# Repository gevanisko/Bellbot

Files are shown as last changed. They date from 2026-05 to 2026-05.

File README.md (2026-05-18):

# BellBot

This repository contains the hardware design files, documentation, and supporting resources for the BellBot project. BellBot is an autonomous luggage transportation robot intended to use sensing, mapping, wireless control, onboard data storage, and motor control to move luggage through indoor environments.

The hardware in this repository is developed across multiple board revisions. Each version is used to test, validate, and improve different parts of the system, including power regulation, peripheral integration, motor control, communication, and future onboard intelligence.

## Project Overview

The long-term goal of BellBot is to create a robotic luggage transportation system capable of navigating indoor environments. The system is designed around Simultaneous Localization and Mapping (SLAM), LiDAR sensing, inertial measurement, Bluetooth control, onboard logging, and multi-directional motor control.

Early board revisions focus on creating a reliable minimum viable product (MVP). Later revisions are intended to improve size, integration, efficiency, and performance.

## Core Goals

The BellBot hardware is designed to support:

- Autonomous navigation through mapped environments
- LiDAR-based obstacle detection and mapping
- Remote control through Bluetooth or another wireless interface
- Onboard storage for sensor data, logs, and system debugging
- Motor control for movement in a 2D plane
- Multiple regulated voltage rails for sensors, logic, and motors
- Expandability for future sensors, memory, and processing hardware

## Hardware Features

Across the project revisions, the BellBot hardware may include:

| Feature | Purpose |
|---|---|
| STM32 Microcontroller | Main control platform for peripherals, motor control, and system logic |
| LiDAR | 2D scanning for mapping, localization, and obstacle detection |
| IMU | Acceleration, angular velocity, magnetic field, and orientation sensing |
| Bluetooth / Wireless Module | Remote control, debugging, or wireless communication |
| SPI Flash / SD Storage | Onboard storage for sensor data and logs |
| Servo / Motor PWM Outputs | Control signals for the robot drive system |
| 3.3 V Rail | Logic-level supply for MCU and low-voltage peripherals |
| 5 V Rail | Peripheral and module power |
| 8 V Rail | Servo or motor power |
| I2C / SPI / UART / Quad-SPI Breakouts | Expansion for additional sensors, memory, or communication modules |
| Battery Charging and Protection | Portable operation and safe lithium-ion battery use |

Later iterations (V2 and onward) are looking to employ AI accelerated MCU chips (STM32 N6) with a reduced size and mainly using SMT components as opposed to through hole components

## Board Revisions

This repository is intended to support multiple hardware revisions. Each revision may include different component choices, layouts, and design improvements.

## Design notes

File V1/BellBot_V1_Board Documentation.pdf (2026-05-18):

# BellBot V1 Board

George Evanisko

May 2026

## 1 Introduction

The objective of BellBot is to incorporate Simultaneous Localization and Mapping (SLAM) alongside other features in order to achieve luggage transportation typically done by a bellboy. This is a difficult task. Therefore, our team decided to first create a minimum viable product (MVP). This is a prototype that limits the number of features to those necessary to demonstrate the basic functionality of the product. For our team, the following criteria were set for the MVP:

- The product can navigate through a pre-mapped obstacle course using LiDAR
- The product can be remotely controlled using Bluetooth
- The product can store all data from operation in onboard memory for further analysis later
- The product can demonstrate maneuverability in all directions on a 2D plane

In order to achieve the criteria for our MVP, a custom printed circuit board (PCB) was designed. Although it may be possible to accomplish the minimum criteria without the use of a custom PCB by using a breadboard or protoboard, a custom PCB was chosen to provide reliable signal integrity, a cleaner aesthetic, and ease of use.
Our custom PCB uses an STM32 Nucleo-F767ZI development board [1], [2] as the main MCU platform, alongside several commercial off-the-shelf (COTS) through-hole components. These components include an inertial measurement unit (IMU), Light Detection and Ranging (LiDAR) unit, Flash SPI memory card for data storage, HC-05 Bluetooth module, four pulse-width modulation (PWM) 8 V continuous-rotation servo pins, as well as additional Quad-SPI and I2C breakout pins to use as needed. At the end of this section, there are 3D renderings of our board. Through-hole COTS components were used for the first iteration due to their ease of soldering, ease of use, and proven reliability. Future iterations of this board will switch to an STM32 SMT chip and SMT components to reduce board size and remove unwanted components.
The 3D modeling/CAD was done in tandem with the board development, and those contents are not covered in this document. This document serves as a datasheet/guide for anyone using the BellBot board. The sections that follow are: (2) Power Systems, which describes how power is distributed throughout the board; (3) Peripherals, which describes how the featured peripherals are connected and used by our MCU; (4) Software Configuration, which shows the STM32CubeMX model and pin configurations used; and (5) Future Improvements, which focuses on future design improvements.

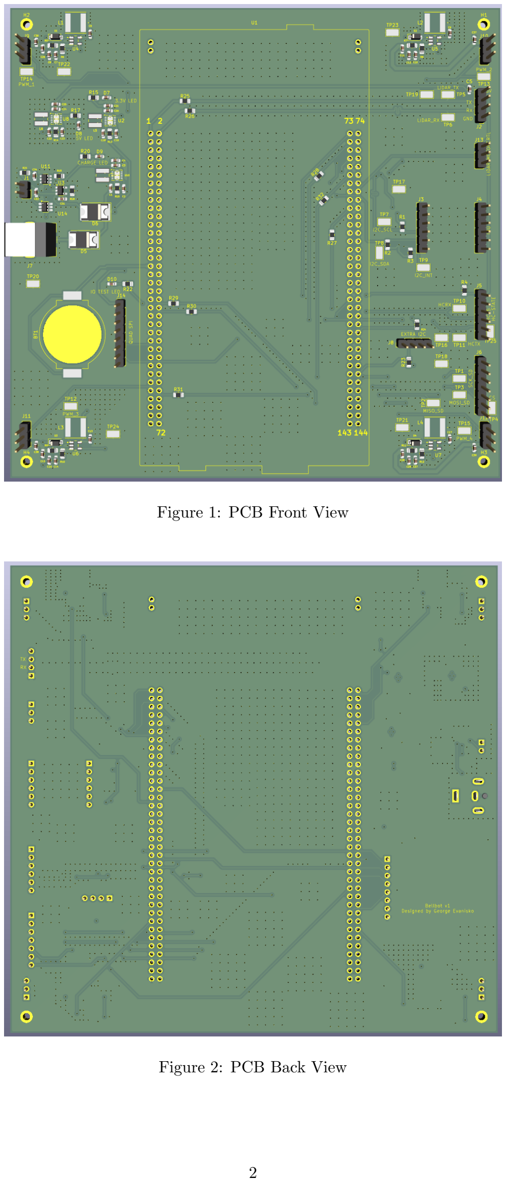
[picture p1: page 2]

Figure 1: PCB Front View

Figure 2: PCB Back View

## 2 Power Systems

Our board features three different voltage levels: 3.3 V, 5 V, and 8 V. The voltage is initially received from a 5 V, 6 A DC power jack input from a wall plug or from a lithium-ion battery. The board uses a simple diode steering method to choose which source to use by employing Schottky diodes to minimize voltage loss. In addition to source control, onboard chips such as the DW01A (U11) [3], along with dual MOSFET FS8205 (U14) [4] chips, are used for battery protection. The board features a separate 5 V charging regulator (U10) that connects directly to the DC power jack and through a lithium-ion charging chip, the MCP73812T (U3) [5], to charge the battery when the DC power jack is being powered by a source greater than the battery’s nominal voltage of 3.3–3.6 V. This means that when using the 5 V, 6 A DC power jack, the battery will always be in charging mode. A table below describes the charging modes:

Mode | DC Power Jack | Battery | Board Operation
DC powered / bat-tery charging | Connected to 5 V wall supply | Charging through the MCP73812T charging circuit | The DC power jack supplies the board power rails while the battery is charged separately. The diode steering circuit pre-vents the battery from being the main supply.
Battery powered | Disconnected | Discharging | The lithium-ion bat-tery supplies the board through the diode steering circuit. The 3.3 V, 5 V, and 8 V rails are generated from the battery input as needed.
Battery protection active | Connected or dis-connected | Protected by DW01A and FS8205 circuit | The protection circuit disconnects or limits the battery path dur-ing unsafe conditions such as over-discharge, overcharge, or overcur-rent. Normal board operation may be interrupted until the fault is removed.

Table 1: Battery and power source operating modes

The U10 5V output regulator is used specifically for charging. The U8 5V output regulator is a general use mainly powering the LiDAR unit.

2.1 8V Boost Converter Inductor and Power Calculations

In terms of power regulators, the board features four 5 V to 8 V switching regulators, each used to power a servo motor. The regulator used is an LT1935 and uses a voltage divider with feedback to determine the output using the following equation:
Vo = 1.265V ∗ (1 + R1
R2
) | (1)

Where R1 and R2 are the resistors used for the feedback voltage divider, as shown by the typical application page:

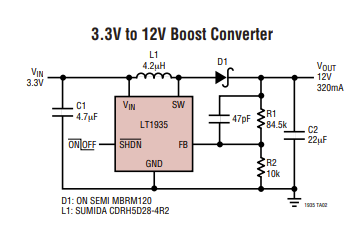
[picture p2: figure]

Figure 3: LT1935 typically application [6]

For our usage, R1 = 56.2K and R2 = 10K yields an output voltage of 8.37 V.
The capacitors are arbitrary and any capacitor can be used if it has a low ESR. The inductor value (L1) is based on the following formula:
L = 3
VIN

VOUT
VOUT − VIN
IMAXf

(2)

Given a maximum switching frequency of 1.2 MHz and an Imax of 2 A with 5 V Vin and 8 V Vout, we can calculate our inductor value as 2.3–2.4 uH, which will be rounded down to 2.2 uH. The output power of the boost converter was also estimated. The output power is related to the input power and converter efficiency, as shown in Equation 3.

POUT = PIN η | (3)

Since input power is equal to input voltage multiplied by input current, this can be written as:

POUT = VIN IIN η | (4)

For this design, the input voltage is 5 V, the maximum input current is approximated using the maximum switch current of 2 A, and the assumed efficiency is 90%.

η = 0.90 | (5)

Substituting the values into Equation 4 gives:

POUT = (5 V)(2 A)(0.90) | (6)
POUT = 9 W | (7)

The output current available from the 8 V rail can then be estimated using the basic power relationship shown in Equation 8.

IOUT =

POUT

VOUT

(8)

Substituting the output power and output voltage gives:

IOUT =

9 W
8 V

(9)

IOUT = 1.125 A | (10)

Based on this estimate, the 8 V boost converter can supply approximately 9 W of output power, corresponding to about 1.1 A at 8 V when powered from the 5 V input. This value is an estimate because the actual output current will depend on the converter efficiency, thermal performance, current limit behavior, and selected external components. In the event that our device is powered by a 3.3-3.6V li-ion battery our output current would be around 0.75 A.

2.2 5V and 3.3V Buck-Boost Converters

For our 5 V and 3.3 V rails, the TPS60001 and TPS60002 were used. The TPS6000X is a 1.8 A switching buck-boost converter. The TPS60001 and TPS60002 have set output voltages of 3.3 V and 5 V, respectively. Below is a typical application schematic:

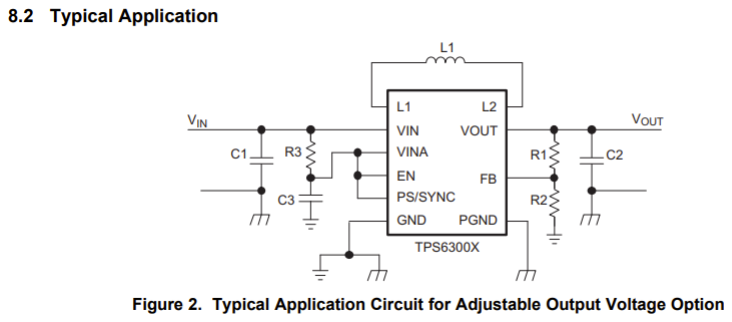
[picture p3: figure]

Figure 4: TPS 6000X Typical Application [7]

For the set output voltage versions, TPS60001 and TPS60002, R1 and R2 are not needed, and the FB pin is shorted to Vout. Using the graphs given by TI, with an input voltage of 5 V, we can expect 1600 mA and 1400 mA output current for the TPS60001 and TPS60002, respectively:

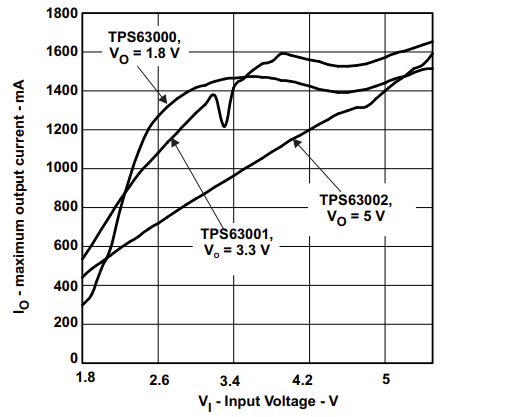
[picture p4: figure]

Figure 5: TPS 6000X Output Voltage [7]

At 3.4 V, which is the approximate voltage level for a lithium-ion battery, we can expect output currents of 1400 mA and 950 mA for the TPS60001 and TPS60002, respectively.

### 2.3 Power Subsystem Bill of Materials

Table 2: Major power subsystem components
Designator | Part Number | Use
U4, U5, U6, U7 | LT1935 | Boost switching regulator used to generate the 8 V rail from the 5 V input. Each LT1935 regulator powers one servo motor.
U2 | TPS60001 | Buck-boost switching regulator used to generate the regulated 3.3 V rail. This rail can be main-tained when powered from either the 5 V DC in-put or the lithium-ion battery.
U8, U10 | TPS60002 | Buck-boost switching regulator used to generate the regulated 5 V rail. This rail can be main-tained when powered from either the DC input or the lithium-ion battery.
U3 | MCP73812T | Lithium-ion battery charging IC used to charge the battery when the external DC power jack is connected.
U11 | DW01A | Lithium-ion battery protection IC used to moni-tor the battery and protect against unsafe con-ditions such as overcharge, over-discharge, and overcurrent.
U14 | FS8205 | Dual MOSFET used with the DW01A battery protection IC to disconnect or protect the battery path during fault conditions.
D5, D6 | Schottky Diode | Used for diode steering between the external DC power jack and the lithium-ion battery. The Schottky diode is used to reduce voltage drop while preventing reverse current between power sources.
J7 | 5 V, 6 A DC Power Jack | Main external power input for the board. When connected, it powers the board and allows the battery charging circuit to charge the lithium-ion battery.
J1 | Lithium-Ion Battery Connector | Backup or portable power source for the board when the external DC power jack is disconnected.
BT1 | Back-up Coin Cell Emergency Power | Backup 3V coin cell battery to preserve data in case of an emergency/unexpected shutdown.

## 3 Peripherals

Our board has four onboard peripheral components: an IMU, LiDAR, memory card, and Bluetooth module. It also has breakout pins for an additional Quad-SPI and I2C peripheral in the event they are needed. There are also four PWM pins, one in each corner, used to control four servo motors. Due to the long length of our transmission lines, 22 Ohm resistors were added in series at the start of each transmission line to prevent ringing.

### 3.1 IMU

Our board uses a through-hole COTS IMU from Adafruit with 9 degrees of freedom (DOF) [8]. This component can communicate over SPI or I2C. I2C was chosen because it uses fewer lines than SPI. This sensor takes a 3.3 V–5 V input and has an active-low reset. It consumes 7.5 mA when active. The functionality of the IMU is listed below:

- Acceleration Vector / Accelerometer: Returns three-axis acceleration data, including both gravity and linear motion, in m/s²
- Angular Velocity Vector / Gyroscope: Returns three-axis rotational speed data in rad/s.

- Magnetic Field Strength Vector / Magnetometer: Returns three-axis magnetic field measurements in microtesla (µT).
- Linear Acceleration Vector: Returns three-axis linear acceleration data with the gravity component removed, in m/s²
- Gravity Vector: Returns three-axis gravitational acceleration data with linear movement removed, in m/s² .
- Absolute Orientation / Rotation Vector: Returns a four-point quaternion output that can be used for accurate orientation tracking and data manipulation.

### 3.2 LiDAR

Our board uses a LiDAR kit from Adafruit, specifically the SLAMTEC RP-LiDAR A1 [9]. This kit communicates via UART, takes 5 V for both LiDAR and servo motor operation, and consumes approximately 600 mA on startup and 450 mA after that. The motor controller uses a GPIO pin to enable motor operation. The pins on the LiDAR do not match one-to-one with the pins on our board. For example, TX and RX are in positions 1 and 2 for the kit but positions 2 and 3 on our board. Please take note of this when setting up the LiDAR. The TX from the board should connect to the RX on the LiDAR and vice versa. Some key features of our LiDAR kit are:

- Provides 360 degree two-dimensional scanning, allowing the system to generate point cloud data for mapping, localization, and obstacle detection.
- Supports a maximum measurement range of up to 12 m for the A1M8-R5 model, with a reduced 6 m range for some earlier A1M8 models.
- Uses laser triangulation to measure distance and outputs both distance and angle data for each sampled point.
- Has a typical scan rate of 5.5 Hz and can be configured up to a maximum scan rate of 10 Hz.
- Supports a sampling frequency of at least 8000 samples per second, allowing the LiDAR to collect dense scan data during operation.
- Outputs sample point data that includes distance, heading angle, measurement quality, and a start flag indicating the beginning of a new scan.
- Uses a low-power infrared laser and is rated as a Class I laser device, making it safe for normal operation when used as specified.
- Includes built-in speed detection and adaptive control, allowing the scanner system to adjust based on the motor speed.
- Includes self-protection and status detection features that can shut down the laser if unsafe or abnormal operating conditions are detected.

The RPLIDAR A1 outputs continuous sample point data frames through its communication interface. Each sample point contains the measured distance in millimeters, the heading angle in degrees, a measurement quality value, and a start flag indicating the beginning of a new scan [9].

Data Field | Unit | Description
Distance | mm | Measured distance between the rotating core of the RPLIDAR A1 and the sampled point.
Heading | Degrees | Current heading angle of the measurement.
Quality Level | Unitless | Indicates the quality of the distance measure-ment.
Start Flag | Boolean | Indicates the start of a new 360 degree scan.

Table 3: RPLIDAR A1 sample point data format

Below is a picture of the LiDAR controls for reference:

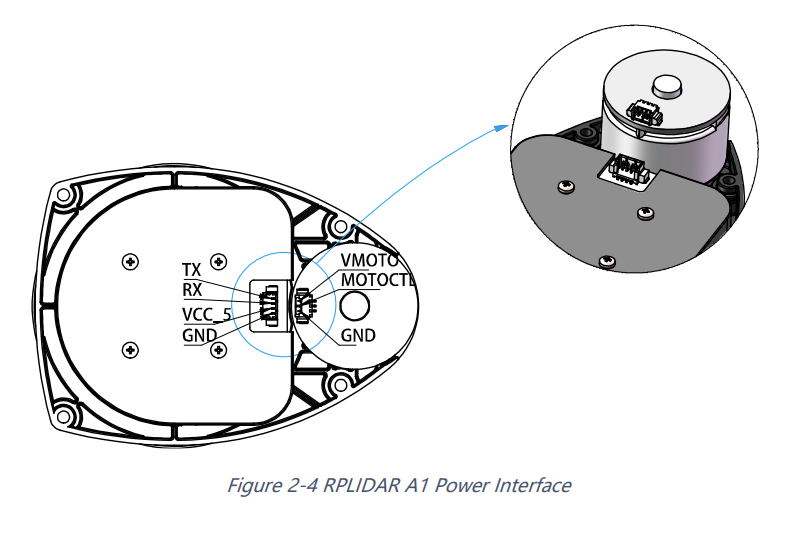
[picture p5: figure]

Figure 6: LIDAR Pinout [9]

### 3.3 SD Flash SPI Memory Card

Our board uses a through-hole COTS SPI Flash SD Card breakout from Adafruit for data storage [10]. The module is designed to behave like an SD card in an SPI flash package, allowing it to be used with standard SD card libraries. This makes it useful for storing sensor data, debug logs, or other information collected by the MCU during operation. This module takes a 3.3 V–5 V input voltage and consumes around 100 mA of current when active.
The SPI Flash SD Card communicates over SPI, using MOSI, MISO, SCK, and CS lines. The breakout supports both 3.3 V and 5 V logic through onboard level shifting and includes a 3.3 V regulator. The CS pin also includes a pull-up resistor, which helps keep the device deselected when the MCU is not actively communicating with it [10]. Some key features of the SPI Flash SD Card are listed below:
- Provides non-volatile data storage, allowing the system to save data even when power is removed.
- Communicates using the SPI interface, requiring MOSI, MISO, SCK, and CS connections to the MCU.
- Can be used with standard SD card libraries, simplifying software integration.
- Supports both 3.3 V and 5 V logic through onboard level shifting.
- Includes an onboard 3.3 V regulator, allowing the module to be powered from the board’s regulated supply.
- Includes a pull-up resistor on the CS pin, helping prevent accidental selection of the device during startup or reset.
- Can be used for storing sensor readings, LiDAR data, IMU data, system logs, or other information generated during operation.

### 3.4 Bluetooth Module

Our board uses a COTS HC-05 Bluetooth module to provide wireless serial communication between the MCU and an external device [11]. The HC-05 communicates using UART, it is powered using 5V but its TX and RX lines are 3.3V TTL. The device consumes about 30mA when active [11].
Some key features of the HC-05 Bluetooth module are listed below:
- Provides wireless serial communication using Bluetooth.
- Can be used to transmit sensor data, system status information, or debug messages to an external device.
- Supports simple point-to-point communication, making it useful for basic wireless control or monitoring.
- Uses a small number of signal lines, requiring only UART TX, UART RX, power, and ground for normal operation.
- Can be configured using AT commands, allowing settings such as the module name, baud rate, and pairing password to be changed.
- Allows the board to send data wirelessly without requiring a USB cable or direct serial connection during testing.

### 3.5 Peripherals Bill of Materials

Designator | Part Number | Use
U1 | STM32 Nucleo-F767ZI | Main MCU development board used to control the system, communicate with peripherals, gen-erate PWM signals, and process sensor data.
J3, J4 | BNO085 | 9-DOF IMU used to measure acceleration, an-gular velocity, magnetic field strength, linear acceleration, gravity, and absolute orientation.
J2, J13 | SLAMTEC RPLIDAR A1 | 360 degree LiDAR sensor used for distance scanning, obstacle detection, mapping, and lo-calization.
J6 | Adafruit SPI Flash SD Card | SPI-based storage module used to save sensor data, LiDAR data, IMU data, debug logs, or other system information.
J5 | HC-05 | Bluetooth serial module used for wireless UART communication between the MCU and an external Bluetooth device.
J9, J10, J11, J12 | Servo PWM Header | Header pins used to provide PWM control sig-nals to the four continuous-rotation servo mo-tors.
J8 | Quad-SPI Breakout Header | Expansion header used to provide access to Quad-SPI signals for future peripherals or memory expansion.
J14 | I2C Breakout Header | Expansion header used to provide access to I2C communication lines for additional sensors or peripherals.

Table 4: Major MCU and peripheral subsystem components

## 4 Software Configuration

Below is the a screenshot from the IOC file being used for this project in CubeMX. The IOC file is included in the GitHub in the STM32CubeData folder.

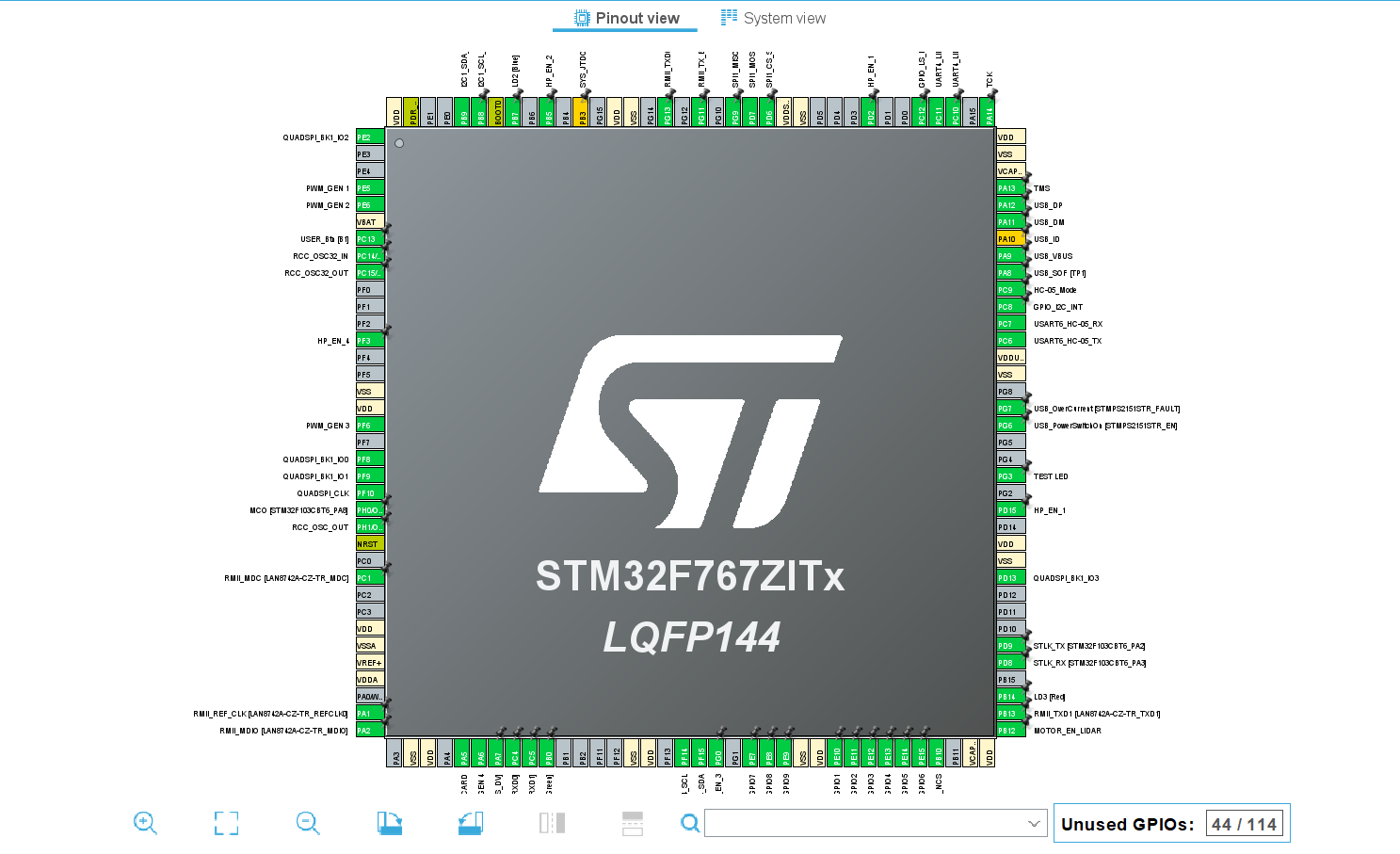
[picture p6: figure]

Figure 7: CubeMX IOC Rendering

## 5 Future Improvements

Future improvements mainly involve a reduction in size by eliminating COTS through-hole components with SMT components. The STM32-F767IZ Nucleo board will be replaced with an STM32 N6 or equivalent QFP/BGA chip with an AI accelerator. The COTS peripherials will be replaced with SMT equivalents. Further improvements will be determined experimentally when the board is assembled and field tested.
One error was found in the board which is the reset pin on the IMU is left floating when it should be pulled-up to high to prevent floating reset (active-LOW reset).
Chip selection (MCU) in future versions will focus on AI acceleration on MCU (using models such as STM32ModelZoo or MCUNet) [12].

## References

[1] STMicroelectronics, STM32 Nucleo-144 Boards: NUCLEO-xxxxLx/xxxxXx/xxxxZx(-P/Q) Data Brief, DB3171, Rev. 18, STMicroelectronics, Nov. 2024. [Online]. Available: https://www.st.com/content/ccc/resource/technical/document/data_brief/group1/8c/c9/8a/9b/3e/f0/45/bb/DM00357737/files/DM00357737.pdf/jcr:content/translations/en.DM00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.
[2] STMicroelectronics, STM32F765xx, STM32F767xx, STM32F768Ax and STM32F769xx: Arm Cortex-M7 32-bit MCU+FPU, 462 DMIPS, up to 2 MB Flash, 512+16+4 KB RAM, USB OTG HS/FS, 28 Communication Interfaces, LCD, DSI, DS11532, Rev. 9, STMicroelectronics, Jul. 2025. [Online]. Available: https://www.st.com/resource/en/datasheet/stm32f767zi.pdf.
[3] Fortune Semiconductor Corporation, DW01A: One Cell Lithium-ion/Polymer Battery Protection IC, Datasheet, SOT-23-6 package, Fortune Semiconductor Corporation. [Online]. Available: https : / / mm . digikey . com / Volume0/opasdata/d220001/medias/docus/7833/DW01A%20SOT-23-6.PDF.

[4] Fortune Semiconductor Corporation, FS8205A: Dual N-Channel Enhancement Mode Power MOSFET, Datasheet, Rev. 1.2, Fortune Semiconductor Corporation, Aug. 2009. [Online]. Available: https://mm.digikey.com/Volume0/opasdata/d220001/medias/docus/7158/5272_FS8205A.pdf.
[5] Microchip Technology Inc., MCP73811/2: Simple, Miniature Single-Cell, Fully Integrated Li-Ion/Li-Polymer Charge Management Controllers, DS22036B, Datasheet, Microchip Technology Inc., 2007. [Online]. Available: https://ww1.microchip.com/downloads/aemDocuments/documents/OTH/ProductDocuments/DataSheets/22036b.pdf.
[6] Analog Devices, LT1935: 2A, 1.2MHz/2.4MHz Step-Up DC/DC Converter, Datasheet, Analog Devices. [Online]. Available: https://www.analog.com/media/en/technical-documentation/data-sheets/1935f.pdf.
[7] Texas Instruments, TPS63000 High Efficient Single Inductor Buck-Boost Converter With 1.8-A Switches, Datasheet, Texas Instruments, 2019. [Online]. Available: https://www.ti.com/lit/ds/symlink/tps63000. pdf.
[8] Adafruit Industries, Adafruit 9-DOF Orientation IMU Fusion Breakout - BNO085, Product guide, Adafruit Industries. [Online]. Available: https : / / cdn - learn . adafruit . com / downloads / pdf / adafruit - 9 - dof -orientation-imu-fusion-breakout-bno085.pdf.
[9] Shanghai Slamtec Co., Ltd., RPLIDAR A1: Low Cost 360 Degree Laser Range Scanner, Introduction and Datasheet, Model A1M8, rev. 2.1, Shanghai Slamtec Co., Ltd., 2018. [Online]. Available: https : / / cdn -shop.adafruit.com/product-files/4010/4010_datasheet.pdf.
[10] Adafruit Industries, Adafruit SPI Flash SD Card, Product guide, Adafruit Industries, 2024. [Online]. Available: https://cdn-learn.adafruit.com/downloads/pdf/adafruit-spi-flash-sd-card.pdf.
[11] ITEAD Studio, HC-05: Bluetooth to Serial Port Module, Datasheet, ITEAD Studio, Jun. 2010. [Online]. Available: https://components101.com/sites/default/files/component_datasheet/HC- 05%20Datasheet. pdf.
[12] J. Lin, W.-M. Chen, Y. Lin, J. Cohn, C. Gan, and S. Han, “Mcunet: Tiny deep learning on iot devices,” arXiv preprint arXiv:2007.10319, 2020.

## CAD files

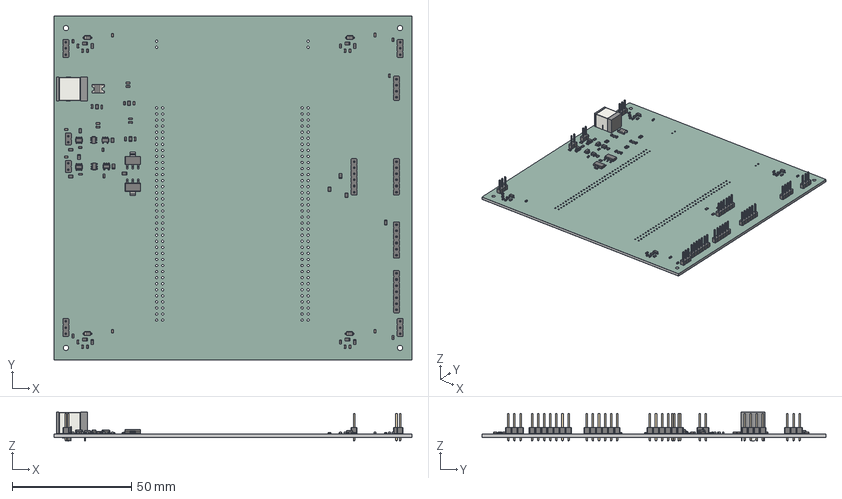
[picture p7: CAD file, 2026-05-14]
V1/PCB/Bellbot.step
150.0 x 144.0 x 12.0 mm
C_0603_1608Metric x 39
R_0805_2012Metric x 22
D_SOD-123 x 4
PinHeader_1x06_P2.54mm_Vertical x 3
SOT-223 x 2
SOT-23-6 x 4
SOT-23-5 x 2
PinHeader_1x04_P2.54mm_Vertical
PinHeader_1x07_P2.54mm_Vertical
PinHeader_1x02_P2.54mm_Vertical x 2
D_2114_3652Metric
PinHeader_1x03_P2.54mm_Vertical x 4
BarrelJack_CUI_PJ-063AH_Horizontal
Bellbot_soldermask
Bellbot_PCB

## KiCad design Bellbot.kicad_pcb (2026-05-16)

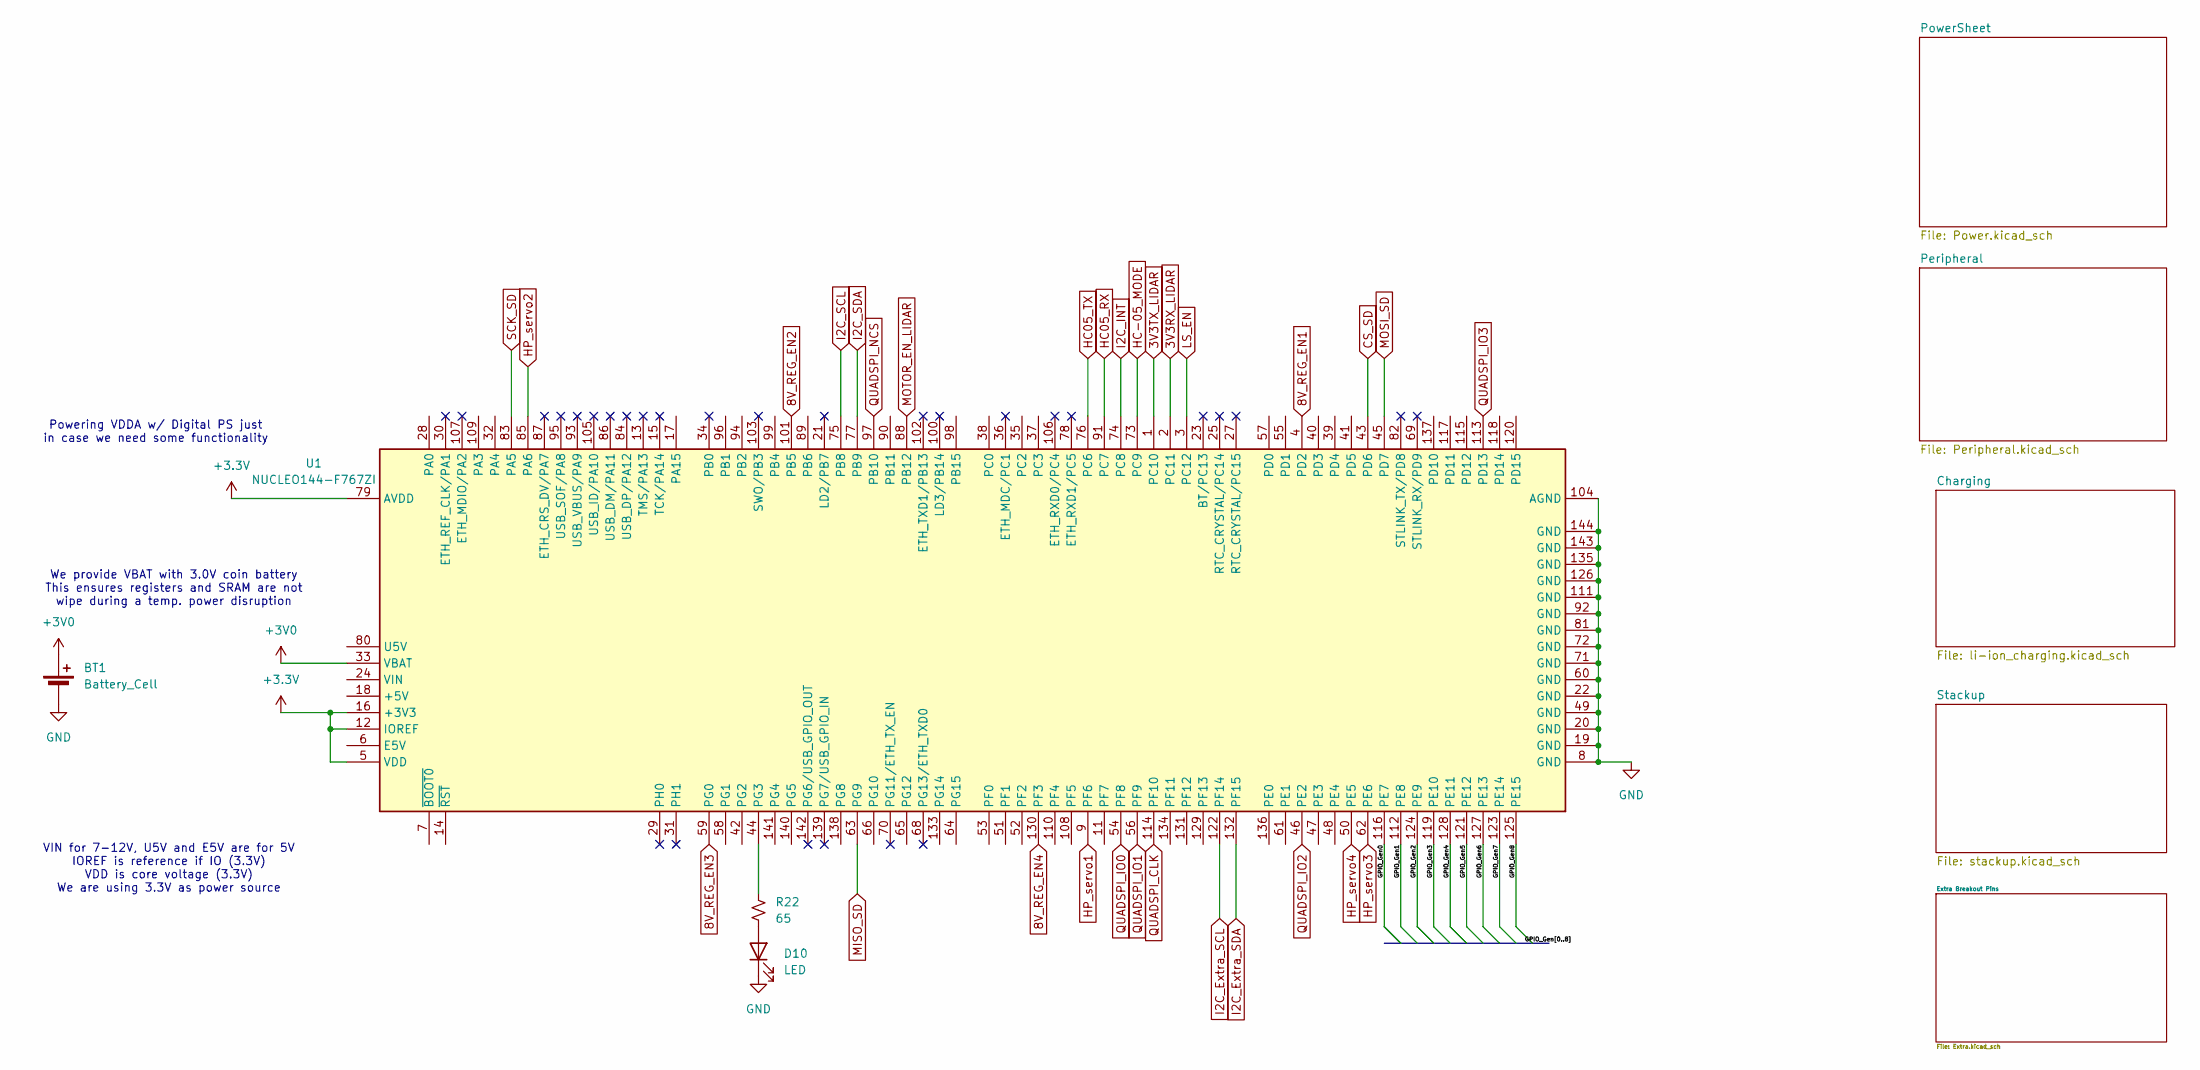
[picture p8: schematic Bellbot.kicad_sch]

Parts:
BT1: Battery_Cell; BatteryHolder_MPD_BC2003_1x2032
D10: LED; C_0603_1608Metric_Pad1.08x0.95mm_HandSolder
R22: 65; R_0805_2012Metric_Pad1.20x1.40mm_HandSolder
U1: NUCLEO144-F767ZI; ST_Morpho_Connector_144_STLink

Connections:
3V3RX_LIDAR: U1.2 (PC11); also elsewhere on the board
3V3TX_LIDAR: U1.1 (PC10); also elsewhere on the board
8V_REG_EN1: U1.4 (PD2); also elsewhere on the board
8V_REG_EN2: U1.101 (PB5); also elsewhere on the board
8V_REG_EN3: U1.59 (PG0); also elsewhere on the board
8V_REG_EN4: U1.130 (PF3); also elsewhere on the board
+3.3V: U1.5 (VDD), U1.12 (IOREF), U1.16 (+3V3), U1.79 (AVDD); also elsewhere on the board
+3V0: BT1.1 (+), U1.33 (VBAT)
/GPIO_Gen0: U1.116 (PE7)
/GPIO_Gen1: U1.112 (PE8)
/GPIO_Gen2: U1.124 (PE9)
/GPIO_Gen3: U1.119 (PE10)
/GPIO_Gen4: U1.128 (PE11)
/GPIO_Gen5: U1.121 (PE12)
/GPIO_Gen6: U1.127 (PE13)
/GPIO_Gen7: U1.123 (PE14)
/GPIO_Gen8: U1.125 (PE15)
CS_SD: U1.43 (PD6); also elsewhere on the board
GND: BT1.2 (-), D10.1 (K), U1.8 (GND), U1.19 (GND), U1.20 (GND), U1.22 (GND), U1.49 (GND), U1.60 (GND), U1.71 (GND), U1.72 (GND), U1.81 (GND), U1.92 (GND), U1.104 (AGND), U1.111 (GND), U1.126 (GND), U1.135 (GND), U1.143 (GND), U1.144 (GND); also elsewhere on the board
HC05_RX: U1.91 (PC7); also elsewhere on the board
HC05_TX: U1.76 (PC6); also elsewhere on the board
HC-05_MODE: U1.73 (PC9); also elsewhere on the board
HP_servo1: U1.9 (PF6); also elsewhere on the board
HP_servo2: U1.85 (PA6); also elsewhere on the board
HP_servo3: U1.62 (PE6); also elsewhere on the board
HP_servo4: U1.50 (PE5); also elsewhere on the board
I2C_Extra_SCL: U1.122 (PF14); also elsewhere on the board
I2C_Extra_SDA: U1.132 (PF15); also elsewhere on the board
I2C_INT: U1.74 (PC8); also elsewhere on the board
I2C_SCL: U1.75 (PB8); also elsewhere on the board
I2C_SDA: U1.77 (PB9); also elsewhere on the board
LS_EN: U1.3 (PC12)
MISO_SD: U1.63 (PG9); also elsewhere on the board
MOSI_SD: U1.45 (PD7); also elsewhere on the board
MOTOR_EN_LIDAR: U1.88 (PB12); also elsewhere on the board
unnamed: D10.2 (A), R22.2
unnamed: R22.1, U1.44 (PG3)
QUADSPI_CLK: U1.114 (PF10); also elsewhere on the board
QUADSPI_IO0: U1.54 (PF8); also elsewhere on the board
QUADSPI_IO1: U1.56 (PF9); also elsewhere on the board
QUADSPI_IO2: U1.46 (PE2); also elsewhere on the board
QUADSPI_IO3: U1.113 (PD13); also elsewhere on the board
QUADSPI_NCS: U1.97 (PB10); also elsewhere on the board
SCK_SD: U1.83 (PA5); also elsewhere on the board

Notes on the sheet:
VIN for 7-12V, U5V and E5V are for 5V IOREF is reference if IO (3.3V) VDD is core voltage (3.3V) We are using 3.3V as power source
Powering VDDA w/ Digital PS just in case we need some functionality
We provide VBAT with 3.0V coin battery This ensures registers and SRAM are not wipe during a temp. power disruption

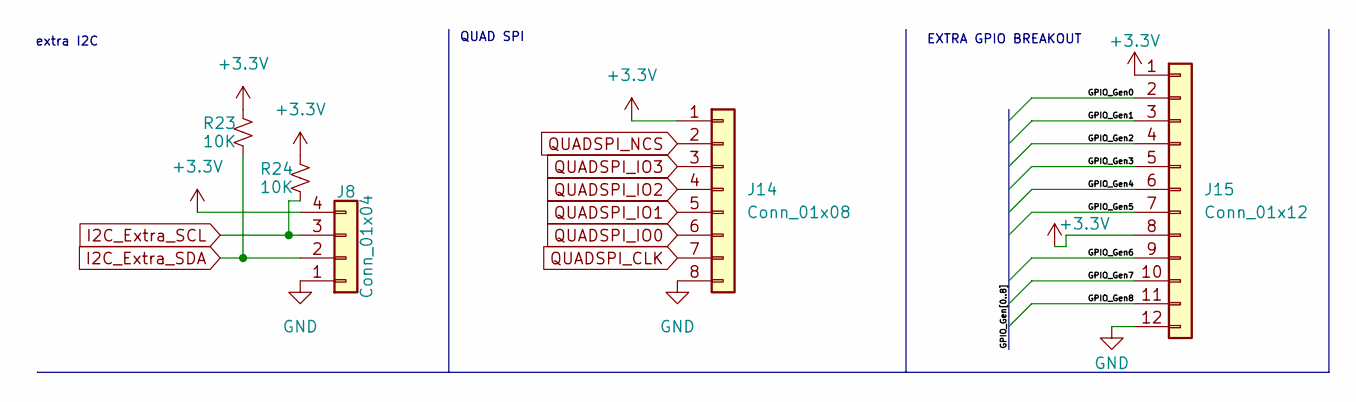
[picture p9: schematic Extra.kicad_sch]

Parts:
J8: Conn_01x04; PinHeader_1x04_P2.54mm_Vertical
J14: Conn_01x08; PinHeader_1x08_P2.54mm_Vertical
J15: Conn_01x12; PinHeader_1x12_P2.54mm_Vertical
R23, R24: 10K; R_0805_2012Metric_Pad1.20x1.40mm_HandSolder

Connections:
+3.3V: J8.4, J14.1, J15.1, J15.8, R23.1, R24.1; also elsewhere on the board
/Extra Breakout Pins/GPIO_Gen0: J15.2
/Extra Breakout Pins/GPIO_Gen1: J15.3
/Extra Breakout Pins/GPIO_Gen2: J15.4
/Extra Breakout Pins/GPIO_Gen3: J15.5
/Extra Breakout Pins/GPIO_Gen4: J15.6
/Extra Breakout Pins/GPIO_Gen5: J15.7
/Extra Breakout Pins/GPIO_Gen6: J15.9
/Extra Breakout Pins/GPIO_Gen7: J15.10
/Extra Breakout Pins/GPIO_Gen8: J15.11
GND: J8.1, J14.8, J15.12; also elsewhere on the board
I2C_Extra_SCL: J8.3, R24.2; also elsewhere on the board
I2C_Extra_SDA: J8.2, R23.2; also elsewhere on the board
QUADSPI_CLK: J14.7; also elsewhere on the board
QUADSPI_IO0: J14.6; also elsewhere on the board
QUADSPI_IO1: J14.5; also elsewhere on the board
QUADSPI_IO2: J14.4; also elsewhere on the board
QUADSPI_IO3: J14.3; also elsewhere on the board
QUADSPI_NCS: J14.2; also elsewhere on the board

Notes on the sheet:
extra I2C
QUAD SPI
EXTRA GPIO BREAKOUT

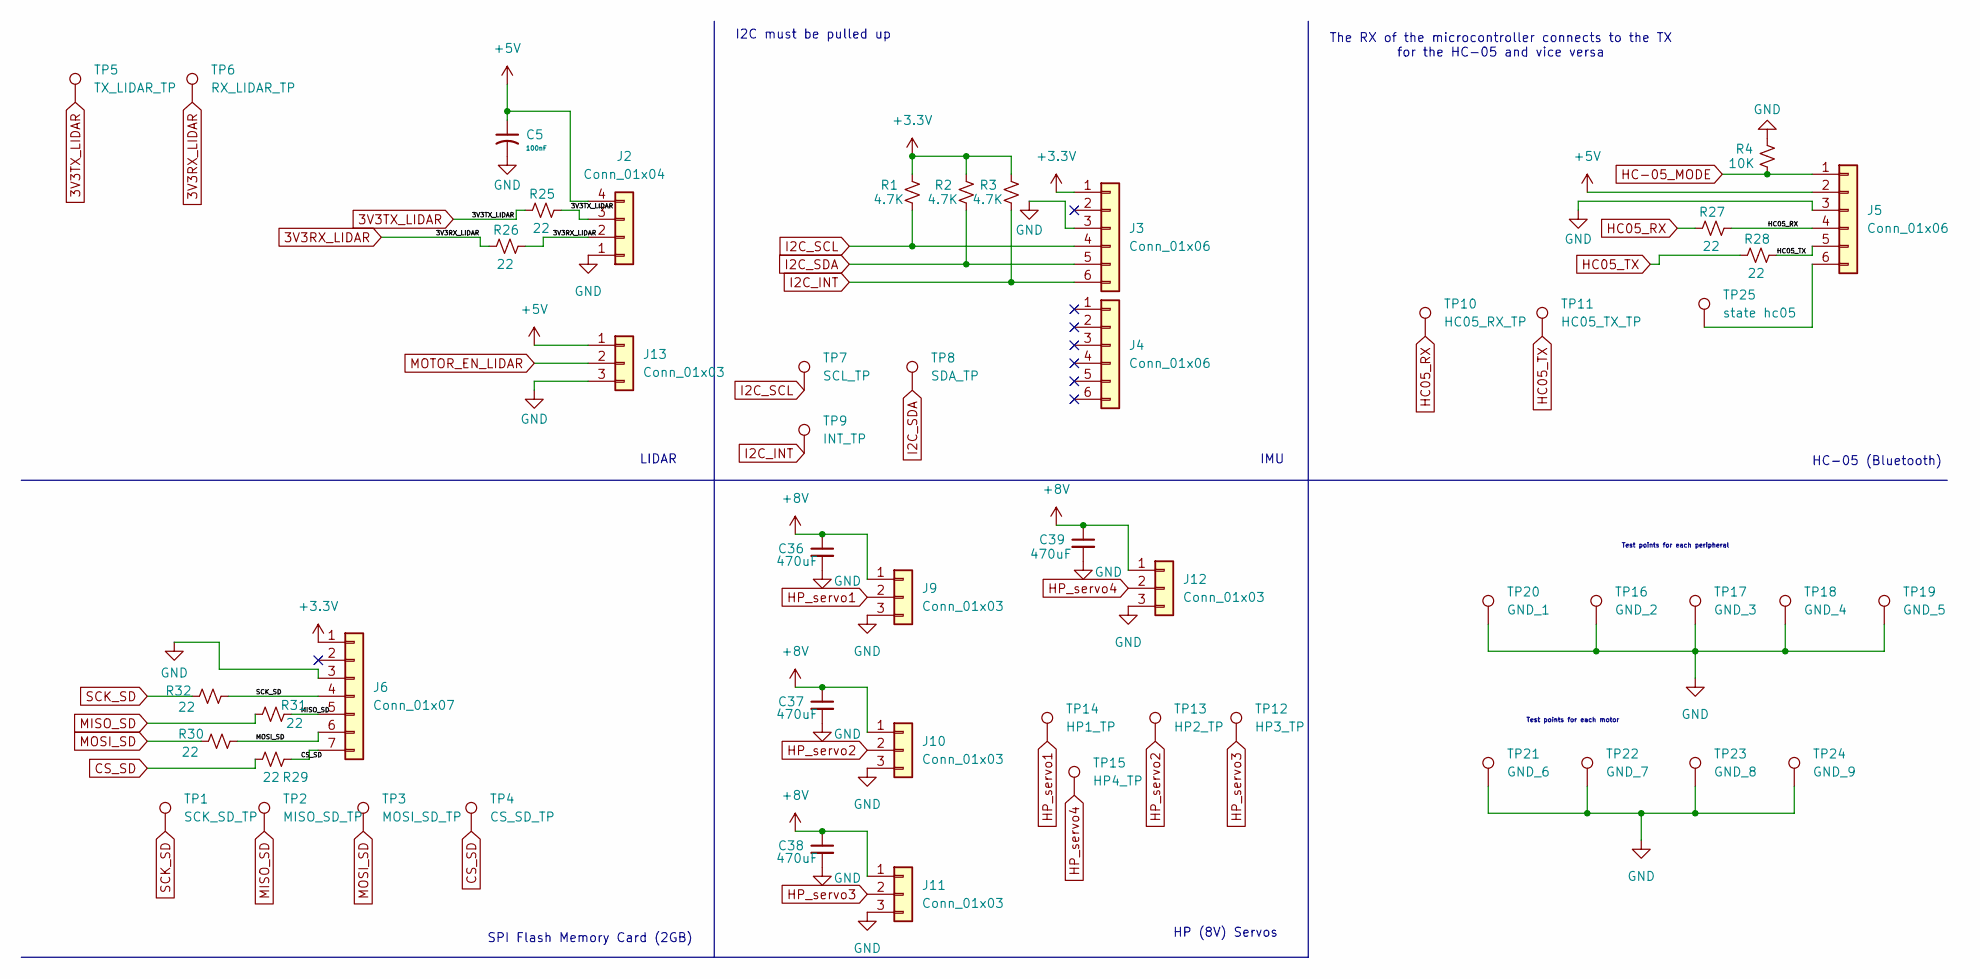
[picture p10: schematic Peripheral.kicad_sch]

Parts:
C5: 100nF; C_0603_1608Metric_Pad1.08x0.95mm_HandSolder
C36, C37, C38, C39: 470uF; C_0603_1608Metric_Pad1.08x0.95mm_HandSolder
J2: Conn_01x04; PinHeader_1x04_P2.54mm_Vertical
J3, J4, J5: Conn_01x06; PinHeader_1x06_P2.54mm_Vertical
J6: Conn_01x07; PinHeader_1x07_P2.54mm_Vertical
J9, J10, J11, J12, J13: Conn_01x03; PinHeader_1x03_P2.54mm_Vertical
R1, R2, R3: 4.7K; R_0805_2012Metric_Pad1.20x1.40mm_HandSolder
R4: 10K; R_0805_2012Metric_Pad1.20x1.40mm_HandSolder
R25, R26, R27, R28, R29, R30, R31, R32: 22; R_0805_2012Metric_Pad1.20x1.40mm_HandSolder
TP1: SCK_SD_TP; TestPoint_Keystone_5019_Miniature
TP2: MISO_SD_TP; TestPoint_Keystone_5019_Miniature
TP3: MOSI_SD_TP; TestPoint_Keystone_5019_Miniature
TP4: CS_SD_TP; TestPoint_Keystone_5019_Miniature
TP5: TX_LIDAR_TP; TestPoint_Keystone_5019_Miniature
TP6: RX_LIDAR_TP; TestPoint_Keystone_5019_Miniature
TP7: SCL_TP; TestPoint_Keystone_5019_Miniature
TP8: SDA_TP; TestPoint_Keystone_5019_Miniature
TP9: INT_TP; TestPoint_Keystone_5019_Miniature
TP10: HC05_RX_TP; TestPoint_Keystone_5019_Miniature
TP11: HC05_TX_TP; TestPoint_Keystone_5019_Miniature
TP12: HP3_TP; TestPoint_Keystone_5019_Miniature
TP13: HP2_TP; TestPoint_Keystone_5019_Miniature
TP14: HP1_TP; TestPoint_Keystone_5019_Miniature
TP15: HP4_TP; TestPoint_Keystone_5019_Miniature
TP16: GND_2; TestPoint_Keystone_5019_Miniature
TP17: GND_3; TestPoint_Keystone_5019_Miniature
TP18: GND_4; TestPoint_Keystone_5019_Miniature
TP19: GND_5; TestPoint_Keystone_5019_Miniature
TP20: GND_1; TestPoint_Keystone_5019_Miniature
TP21: GND_6; TestPoint_Keystone_5019_Miniature
TP22: GND_7; TestPoint_Keystone_5019_Miniature
TP23: GND_8; TestPoint_Keystone_5019_Miniature
TP24: GND_9; TestPoint_Keystone_5019_Miniature
TP25: state hc05; TestPoint_Keystone_5019_Miniature

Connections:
3V3RX_LIDAR: J2.2, R26.1, R26.2, TP6.1 (1_1); also elsewhere on the board
3V3TX_LIDAR: J2.3, R25.1, R25.2, TP5.1 (1_1); also elsewhere on the board
+3.3V: J3.1, J6.1, R1.1, R2.1, R3.1; also elsewhere on the board
+5V: C5.1, J2.4, J5.2, J13.1; also elsewhere on the board
+8V: C36.1, C37.1, C38.1, C39.1, J9.1, J10.1, J11.1, J12.1; also elsewhere on the board
CS_SD: J6.7, R29.1, R29.2, TP4.1 (1_1); also elsewhere on the board
GND: C5.2, C36.2, C37.2, C38.2, C39.2, J2.1, J3.3, J5.3, J6.3, J9.3, J10.3, J11.3, J12.3, J13.3, R4.1, TP16.1 (1_1), TP17.1 (1_1), TP18.1 (1_1), TP19.1 (1_1), TP20.1 (1_1), TP21.1 (1_1), TP22.1 (1_1), TP23.1 (1_1), TP24.1 (1_1); also elsewhere on the board
HC05_RX: J5.4, R27.1, R27.2, TP10.1 (1_1); also elsewhere on the board
HC05_TX: J5.5, R28.1, R28.2, TP11.1 (1_1); also elsewhere on the board
HC-05_MODE: J5.1, R4.2; also elsewhere on the board
HP_servo1: J9.2, TP14.1 (1_1); also elsewhere on the board
HP_servo2: J10.2, TP13.1 (1_1); also elsewhere on the board
HP_servo3: J11.2, TP12.1 (1_1); also elsewhere on the board
HP_servo4: J12.2, TP15.1 (1_1); also elsewhere on the board
I2C_INT: J3.6, R3.2, TP9.1 (1_1); also elsewhere on the board
I2C_SCL: J3.4, R1.2, TP7.1 (1_1); also elsewhere on the board
I2C_SDA: J3.5, R2.2, TP8.1 (1_1); also elsewhere on the board
MISO_SD: J6.5, R31.1, R31.2, TP2.1 (1_1); also elsewhere on the board
MOSI_SD: J6.6, R30.1, R30.2, TP3.1 (1_1); also elsewhere on the board
MOTOR_EN_LIDAR: J13.2; also elsewhere on the board
unnamed: J5.6, TP25.1
SCK_SD: J6.4, R32.1, R32.2, TP1.1 (1_1); also elsewhere on the board

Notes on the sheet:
HC-05 (Bluetooth)
Test points for each motor
The RX of the microcontroller connects to the TX for the HC-05 and vice versa
Test points for each peripheral
IMU
LIDAR
HP (8V) Servos
I2C must be pulled up
SPI Flash Memory Card (2GB)

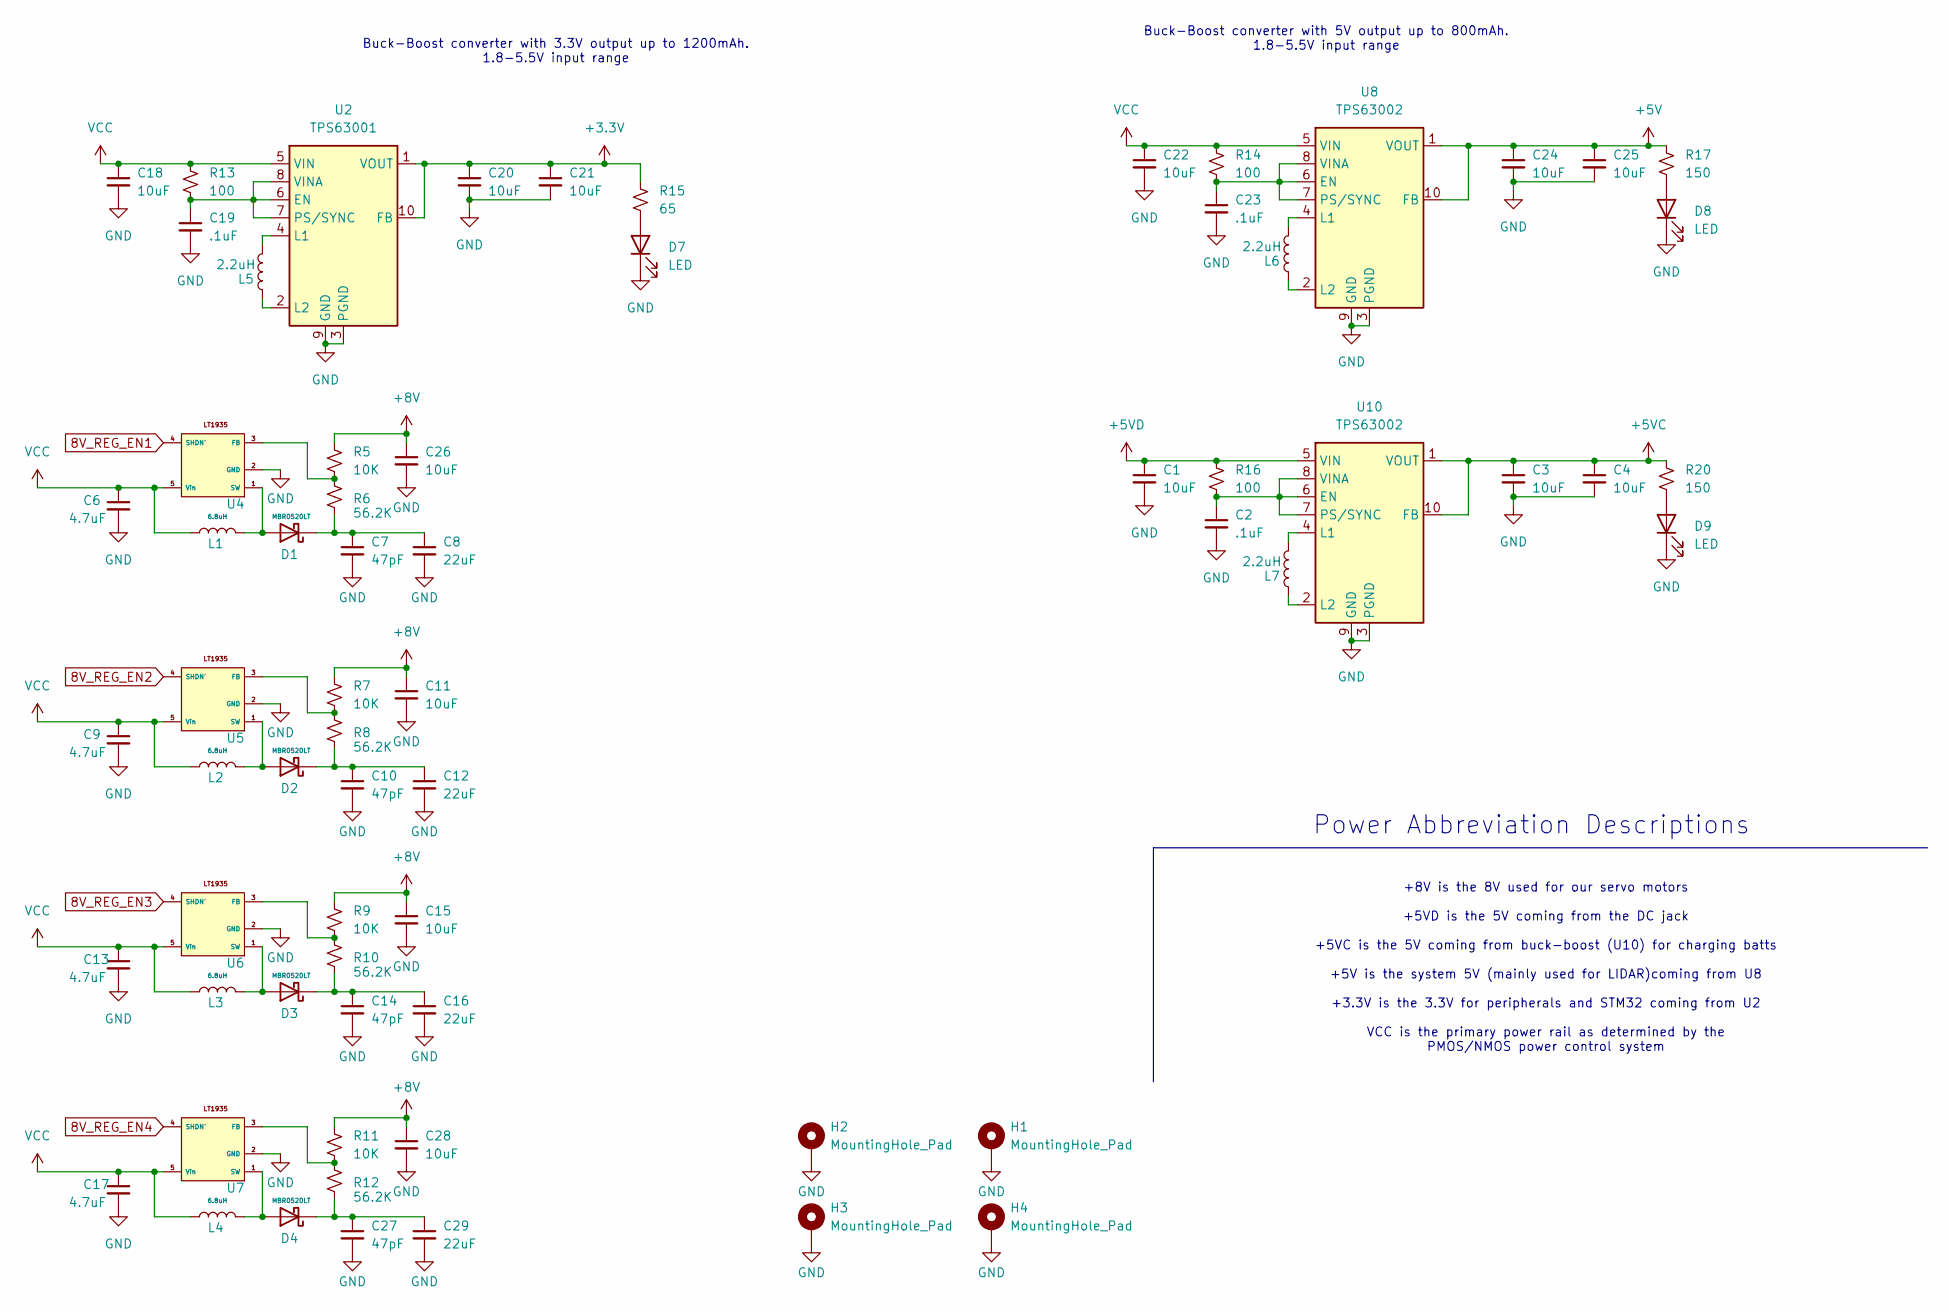
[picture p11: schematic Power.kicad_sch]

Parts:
C1, C3, C4, C11, C15, C18, C20, C21, C22, C24, C25, C26, C28: 10uF; C_0603_1608Metric_Pad1.08x0.95mm_HandSolder
C2, C19, C23: .1uF; C_0603_1608Metric_Pad1.08x0.95mm_HandSolder
C6, C9, C13, C17: 4.7uF; C_0603_1608Metric_Pad1.08x0.95mm_HandSolder
C7, C10, C14, C27: 47pF; C_0603_1608Metric_Pad1.08x0.95mm_HandSolder
C8, C12, C16, C29: 22uF; C_0603_1608Metric_Pad1.08x0.95mm_HandSolder
D1, D2, D3, D4: MBR0520LT; D_SOD-123
D7, D8, D9: LED; C_0603_1608Metric_Pad1.08x0.95mm_HandSolder
H1, H2, H3, H4: MountingHole_Pad; MountingHole_2.2mm_M2_DIN965_Pad
L1, L2, L3, L4: 6.8uH; NR6020T6R8
L5, L6, L7: 2.2uH; IND_VLS4012ET-2R2M-CA
R5, R7, R9, R11: 10K; R_0805_2012Metric_Pad1.20x1.40mm_HandSolder
R6, R8, R10, R12: 56.2K; R_0805_2012Metric_Pad1.20x1.40mm_HandSolder
R13, R14, R16: 100; R_0805_2012Metric_Pad1.20x1.40mm_HandSolder
R15: 65; R_0805_2012Metric_Pad1.20x1.40mm_HandSolder
R17, R20: 150; R_0805_2012Metric_Pad1.20x1.40mm_HandSolder
U2: TPS63001; Texas_DRC0010J_ThermalVias
U4, U5, U6, U7: LT1935
U8, U10: TPS63002; Texas_DRC0010J_ThermalVias

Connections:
8V_REG_EN1: U4.4 (SHDN'); also elsewhere on the board
8V_REG_EN2: U5.4 (SHDN'); also elsewhere on the board
8V_REG_EN3: U6.4 (SHDN'); also elsewhere on the board
8V_REG_EN4: U7.4 (SHDN'); also elsewhere on the board
+3.3V: C20.1, C21.1, R15.1, U2.1 (VOUT), U2.10 (FB); also elsewhere on the board
+5V: C24.1, C25.1, R17.1, U8.1 (VOUT), U8.10 (FB); also elsewhere on the board
+5VC: C3.1, C4.1, R20.1, U10.1 (VOUT), U10.10 (FB); also elsewhere on the board
+5VD: C1.1, C6.1, C9.1, C13.1, C17.1, C18.1, C22.1, L1.1, L2.1, L3.1, L4.1, R13.1, R14.1, R16.1, U2.5 (VIN), U4.5 (Vin), U5.5 (Vin), U6.5 (Vin), U7.5 (Vin), U8.5 (VIN), U10.5 (VIN); also elsewhere on the board
+8V: C11.1, C15.1, C26.1, C28.1, R5.1, R7.1, R9.1, R11.1; also elsewhere on the board
GND: C1.2, C2.2, C3.2, C4.2, C6.2, C7.2, C8.2, C9.2, C10.2, C11.2, C12.2, C13.2, C14.2, C15.2, C16.2, C17.2, C18.2, C19.2, C20.2, C21.2, C22.2, C23.2, C24.2, C25.2, C26.2, C27.2, C28.2, C29.2, D7.1 (K), D8.1 (K), D9.1 (K), H1.1 (1_1), H2.1 (1_1), H3.1 (1_1), H4.1 (1_1), U2.3 (PGND), U2.9 (GND), U2.11 (PGND), U4.2 (GND), U5.2 (GND), U6.2 (GND), U7.2 (GND), U8.3 (PGND), U8.9 (GND), U8.11 (PGND), U10.3 (PGND), U10.9 (GND), U10.11 (PGND); also elsewhere on the board
unnamed: D1.2 (A), L1.2, U4.1 (SW)
unnamed: C7.1, C8.1, D1.1 (K), R6.2
unnamed: D2.2 (A), L2.2, U5.1 (SW)
unnamed: C10.1, C12.1, D2.1 (K), R8.2
unnamed: D3.2 (A), L3.2, U6.1 (SW)
unnamed: C14.1, C16.1, D3.1 (K), R10.2
unnamed: D4.2 (A), L4.2, U7.1 (SW)
unnamed: C27.1, C29.1, D4.1 (K), R12.2
unnamed: D7.2 (A), R15.2
unnamed: D8.2 (A), R17.2
unnamed: D9.2 (A), R20.2
unnamed: C19.1, R13.2, U2.6 (EN), U2.7 (PS/SYNC), U2.8 (VINA)
unnamed: L5.2, U2.4 (L1)
unnamed: L5.1, U2.2 (L2)
unnamed: R5.2, R6.1, U4.3 (FB)
unnamed: R7.2, R8.1, U5.3 (FB)
unnamed: R9.2, R10.1, U6.3 (FB)
unnamed: R11.2, R12.1, U7.3 (FB)
unnamed: C23.1, R14.2, U8.6 (EN), U8.7 (PS/SYNC), U8.8 (VINA)
unnamed: L6.2, U8.4 (L1)
unnamed: L6.1, U8.2 (L2)
unnamed: C2.1, R16.2, U10.6 (EN), U10.7 (PS/SYNC), U10.8 (VINA)
unnamed: L7.2, U10.4 (L1)
unnamed: L7.1, U10.2 (L2)

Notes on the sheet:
Buck-Boost converter with 3.3V output up to 1200mAh. 1.8-5.5V input range
+8V is the 8V used for our servo motors +5VD is the 5V coming from the DC jack +5VC is the 5V coming from buck-boost (U10) for charging batts +5V is the system 5V (mainly used for LIDAR)coming from U8 +3.3V is the 3.3V for peripherals and STM32 coming from U2 VCC is the primary power rail as determ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
Power Abbreviation Descriptions
Buck-Boost converter with 5V output up to 800mAh. 1.8-5.5V input range

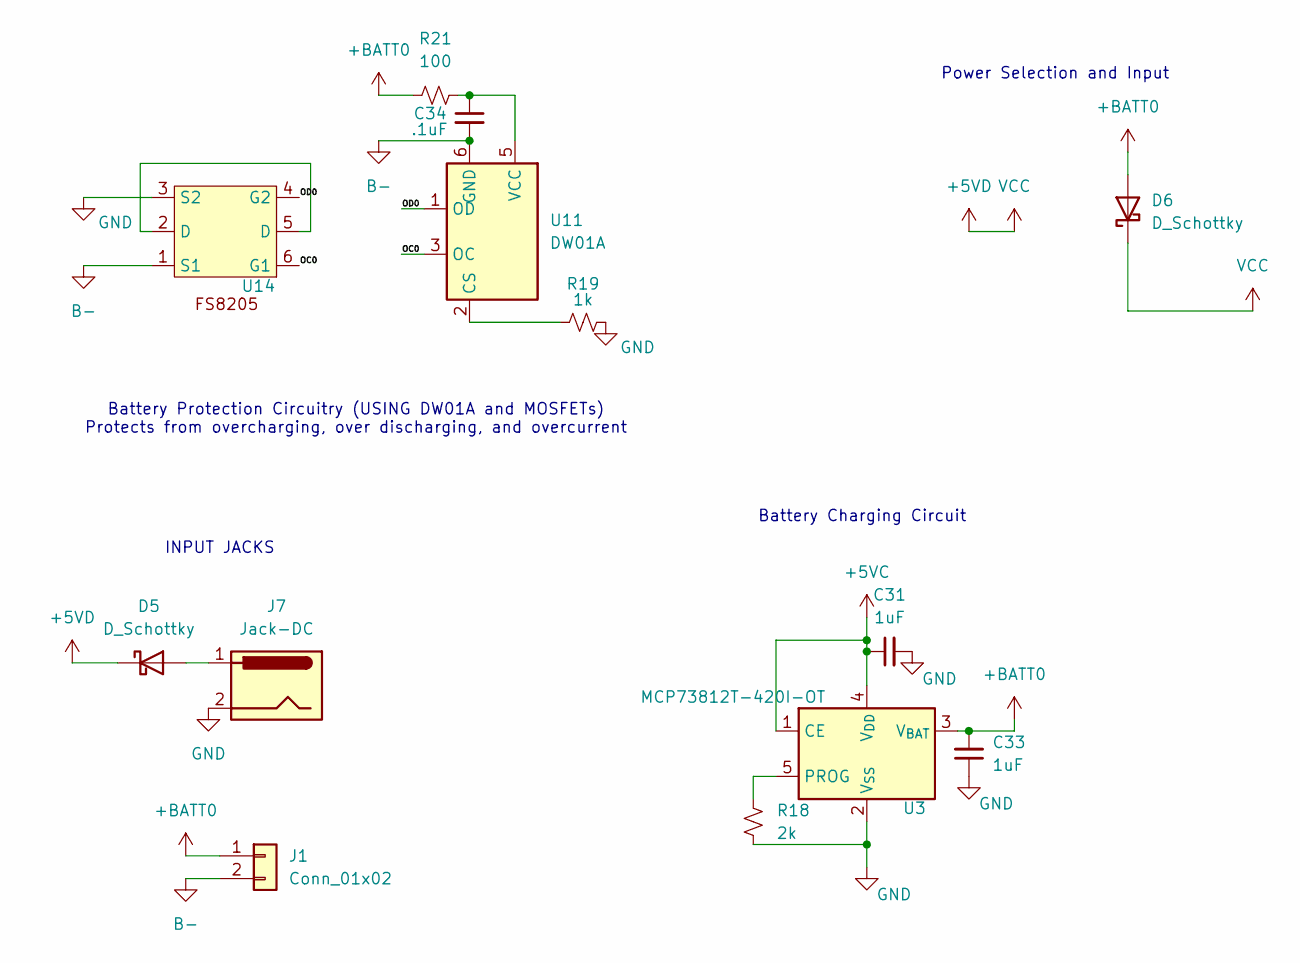
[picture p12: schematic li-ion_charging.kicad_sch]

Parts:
C31, C33: 1uF; C_0603_1608Metric_Pad1.08x0.95mm_HandSolder
C34: .1uF; C_0603_1608Metric_Pad1.08x0.95mm_HandSolder
D5, D6: D_Schottky; D_3220_8050Metric_Pad2.65x5.15mm_HandSolder
J1: Conn_01x02; PinHeader_1x02_P2.54mm_Vertical
J7: Jack-DC; BarrelJack_CUI_PJ-063AH_Horizontal
R18: 2k; R_0805_2012Metric_Pad1.20x1.40mm_HandSolder
R19: 1k; R_0805_2012Metric_Pad1.20x1.40mm_HandSolder
R21: 100; R_0805_2012Metric_Pad1.20x1.40mm_HandSolder
U3: MCP73812T-420I-OT; SOT-23-5
U11: DW01A; SOT-23-6
U14: SOT-23-6_Handsoldering

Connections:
+5VC: C31.1, U3.1 (CE), U3.4 (V_{DD}); also elsewhere on the board
+5VD: D5.1 (K), D6.1 (K); also elsewhere on the board
+BATT0: C33.2, D6.2 (A), J1.1, R21.1, U3.3 (V_{BAT})
/Charging/OC0: U11.3 (OC), U14.6 (G1)
/Charging/OD0: U11.1 (OD), U14.4 (G2)
B-: C34.2, J1.2, U11.6 (GND), U14.1 (S1)
GND: C31.2, C33.1, J7.2, R18.2, R19.2, U3.2 (V_{SS}), U14.3 (S2); also elsewhere on the board
unnamed: D5.2 (A), J7.1
unnamed: R18.1, U3.5 (PROG)
unnamed: R19.1, U11.2 (CS)
unnamed: C34.1, R21.2, U11.5 (VCC)
unnamed: U14.2 (D), U14.5 (D)

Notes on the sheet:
Battery Protection Circuitry (USING DW01A and MOSFETs) Protects from overcharging, over discharging, and overcurrent
Battery Charging Circuit
Power Selection and Input
INPUT JACKS

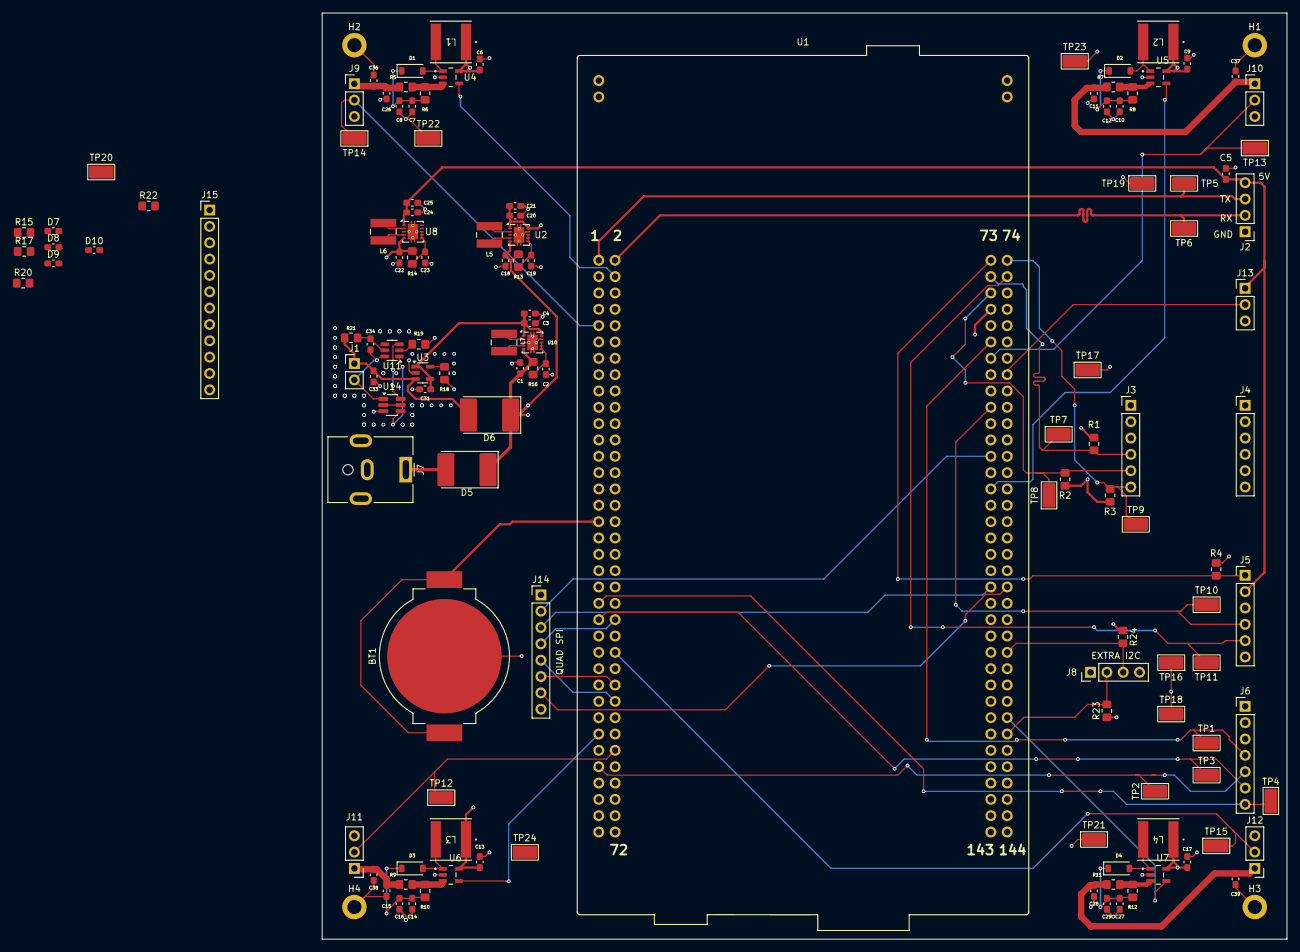
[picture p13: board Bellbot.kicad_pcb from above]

Board: 4 copper layers, 150.0 x 144.0 mm, 132 parts (0 on the bottom side), 71 nets.

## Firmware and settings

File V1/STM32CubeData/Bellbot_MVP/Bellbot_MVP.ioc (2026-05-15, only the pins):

Mcu.UserName=STM32F767ZITx
PA1.GPIO_Label=RMII_REF_CLK [LAN8742A-CZ-TR_REFCLK0]
PA1.Signal=ETH_REF_CLK
PA10.GPIO_Label=USB_ID
PA10.Signal=USB_OTG_FS_ID
PA11.GPIO_Label=USB_DM
PA11.Signal=USB_OTG_FS_DM
PA12.GPIO_Label=USB_DP
PA12.Signal=USB_OTG_FS_DP
PA13.GPIO_Label=TMS
PA13.Signal=SYS_JTMS-SWDIO
PA14.GPIO_Label=TCK
PA14.Signal=SYS_JTCK-SWCLK
PA2.GPIO_Label=RMII_MDIO [LAN8742A-CZ-TR_MDIO]
PA2.Signal=ETH_MDIO
PA5.GPIO_Label=SPI1_SCK-SDCARD
PA5.Signal=SPI1_SCK
PA6.GPIO_Label=PWM_GEN 4
PA6.Signal=S_TIM13_CH1
PA7.GPIO_Label=RMII_CRS_DV [LAN8742A-CZ-TR_CRS_DV]
PA7.Signal=ETH_CRS_DV
PA8.GPIO_Label=USB_SOF [TP1]
PA8.Signal=USB_OTG_FS_SOF
PA9.GPIO_Label=USB_VBUS
PA9.Signal=USB_OTG_FS_VBUS
PB0.GPIO_Label=LD1 [Green]
PB0.Signal=GPIO_Output
PB10.Signal=QUADSPI_BK1_NCS
PB12.GPIO_Label=MOTOR_EN_LIDAR
PB12.Signal=GPIO_Output
PB13.GPIO_Label=RMII_TXD1 [LAN8742A-CZ-TR_TXD1]
PB13.Signal=ETH_TXD1
PB14.GPIO_Label=LD3 [Red]
PB14.Signal=GPIO_Output
PB3.Signal=SYS_JTDO-SWO
PB5.GPIO_Label=HP_EN_2
PB5.Signal=GPIO_Output
PB7.GPIO_Label=LD2 [Blue]
PB7.Signal=GPIO_Output
PB8.GPIO_Label=I2C1_SCL_IMU
PB8.Signal=I2C1_SCL
PB9.GPIO_Label=I2C1_SDA_IMU
PB9.Signal=I2C1_SDA
PC1.GPIO_Label=RMII_MDC [LAN8742A-CZ-TR_MDC]
PC1.Signal=ETH_MDC
PC10.GPIO_Label=UART4_LiDAR_TX
PC10.Signal=UART4_TX
PC11.GPIO_Label=UART4_LiDAR_RX
PC11.Signal=UART4_RX
PC12.GPIO_Label=GPIO_LS_EN
PC12.Signal=GPIO_Output
PC13.GPIO_Label=USER_Btn [B1]
PC13.Signal=GPXTI13
PC14/OSC32_IN.Signal=RCC_OSC32_IN
PC15/OSC32_OUT.Signal=RCC_OSC32_OUT
PC4.GPIO_Label=RMII_RXD0 [LAN8742A-CZ-TR_RXD0]
PC4.Signal=ETH_RXD0
PC5.GPIO_Label=RMII_RXD1 [LAN8742A-CZ-TR_RXD1]
PC5.Signal=ETH_RXD1
PC6.GPIO_Label=USART6_HC-05_TX
PC6.Signal=USART6_TX
PC7.GPIO_Label=USART6_HC-05_RX
PC7.Signal=USART6_RX
PC8.GPIO_Label=GPIO_I2C_INT
PC8.Signal=GPXTI8
PC9.GPIO_Label=HC-05_Mode
PC9.Signal=GPIO_Output
PD13.Signal=QUADSPI_BK1_IO3
PD15.GPIO_Label=HP_EN_1
PD15.Signal=GPIO_Output
PD2.GPIO_Label=HP_EN_1
PD2.Signal=GPIO_Output
PD6.GPIO_Label=SPI1_CS_SDCARD
PD6.Signal=GPIO_Output
PD7.GPIO_Label=SPI1_MOSI_SDCARD
PD7.Signal=SPI1_MOSI
PD8.GPIO_Label=STLK_RX [STM32F103CBT6_PA3]
PD8.Signal=USART3_TX
PD9.GPIO_Label=STLK_TX [STM32F103CBT6_PA2]
PD9.Signal=USART3_RX
PE10.GPIO_Label=Gen_GPIO1
PE10.Signal=GPIO_Output
PE11.GPIO_Label=Gen_GPIO2
PE11.Signal=GPIO_Output
PE12.GPIO_Label=Gen_GPIO3
PE12.Signal=GPIO_Output
PE13.GPIO_Label=Gen_GPIO4
PE13.Signal=GPIO_Output
PE14.GPIO_Label=Gen_GPIO5
PE14.Signal=GPIO_Output
PE15.GPIO_Label=Gen_GPIO6
PE15.Signal=GPIO_Output
PE2.Signal=QUADSPI_BK1_IO2
PE5.GPIO_Label=PWM_GEN 1
PE5.Signal=S_TIM9_CH1
PE6.GPIO_Label=PWM_GEN 2
PE6.Signal=S_TIM9_CH2
PE7.GPIO_Label=Gen_GPIO7
PE7.Signal=GPIO_Output
PE8.GPIO_Label=Gen_GPIO8
PE8.Signal=GPIO_Output
PE9.GPIO_Label=Gen_GPIO9
PE9.Signal=GPIO_Output
PF10.Signal=QUADSPI_CLK
PF14.Signal=I2C4_SCL
PF15.Signal=I2C4_SDA
PF3.GPIO_Label=HP_EN_4
PF3.Signal=GPIO_Output
PF6.GPIO_Label=PWM_GEN 3
PF6.Signal=S_TIM10_CH1
PF8.Signal=QUADSPI_BK1_IO0
PF9.Signal=QUADSPI_BK1_IO1
PG0.GPIO_Label=HP_EN_3
PG0.Signal=GPIO_Output
PG11.GPIO_Label=RMII_TX_EN [LAN8742A-CZ-TR_TXEN]
PG11.Signal=ETH_TX_EN
PG13.GPIO_Label=RMII_TXD0 [LAN8742A-CZ-TR_TXD0]
PG13.Signal=ETH_TXD0
PG3.GPIO_Label=TEST LED
PG3.Signal=GPIO_Output
PG6.GPIO_Label=USB_PowerSwitchOn [STMPS2151STR_EN]
PG6.Signal=GPIO_Output
PG7.GPIO_Label=USB_OverCurrent [STMPS2151STR_FAULT]
PG7.Signal=GPIO_Input
PG9.GPIO_Label=SPI1_MISO_SDCARD
PG9.Signal=SPI1_MISO
PH0/OSC_IN.GPIO_Label=MCO [STM32F103CBT6_PA8]
PH0/OSC_IN.Signal=RCC_OSC_IN
PH1/OSC_OUT.Signal=RCC_OSC_OUT

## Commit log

2026-05-14 stm32cubeide files added
    [Bellbot.kicad_pcb]
2026-05-14 General Layout Complete
    Completed general layout, beginning to add debugging components such as test points and
    [Bellbot.kicad_pcb, Bellbot.kicad_sch, Peripheral.kicad_sch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]
2026-05-15 update
    more work on testpoints
    [Peripheral.kicad_sch]
2026-05-15 testpoints on board
    Organized testpoints on board. Still need to fix bus for general purpose GPIO and route traces for LEDs.
    [Bellbot.kicad_pcb, Bellbot.kicad_sch, Extra.kicad_sch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]
2026-05-15 STM32 MX IoC update
    Still need to rename Gen GPIO pins to new bus names
2026-05-16 routed quad spi
    [Bellbot.kicad_pcb]
2026-05-16 almost completed board
    need to clean up silkscreen, run thru checklist and verify, review datasheets
    [Extra.kicad_sch, Peripheral.kicad_sch]
2026-05-17 completed v1 board with outputs
    [Bellbot-B_Cu.gbr, Bellbot-B_Mask.gbr, Bellbot-B_Paste.gbr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]
2026-05-17 cleanup and reorganizing
    [Bellbot-B_Cu.gbr, Bellbot-B_Mask.gbr, Bellbot-B_Paste.gbr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]
2026-05-18 Updated/Verified Values
    [Peripheral.kicad_sch, Power.kicad_sch]
